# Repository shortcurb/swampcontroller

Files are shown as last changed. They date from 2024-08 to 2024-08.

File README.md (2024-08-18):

# swampcontroller
Hardware and software for controlling evaporative coolers with MQTT and relays

I live in a climate where using evaporative (swamp) coolers to cool dwellings is a generally effective possibility. I have two swamp coolers. I like them because they are cheap to run, cheap and easy to maintain, and if one breaks, I can almost certainly fix it myself, rather than calling a contractor.

My swamp coolers electrical components consist of a water pump and a 1/4HP blower fan with high and low speed settings. I designed this PCB to use an ESP8266 to control three off-board 12V automotive relays, which was easier than trying to figure out how to manage 10A on my little 1oz copper PCB traces.

If anyone is interested, I have 3 remaining unpopulated PCB boards I would be happy to sell/ship somewhere

Hardware features:
* ESP8266 header
* LM2596 (eBay/Amazon THT variant) 4V-40V input
* power header
* 3 relay-control headers

Hardware Problems:
* The pins that control speedheader and fanheader are currently wired to pins that control the flash on an ESP8266. Need to cut the trace and install a jumper wire somewhere else to control them correctly.

Software features:
* State, command, and response MQTT feeds
* State feed publishes the state of the swamper regularly
* Subscribes to command feed to listen for commands
* Response feed is for sending responses to commands
* 5s delay after receiving a command, to prevent changing motor/pump electricity too quickly
Software Problems:
* If the MQTT broker goes down, or Wifi goes down, the device will eventually crash and turn off the blower and fan. This is intended as a purely wifi-controllable device, so its user preference to decide whether failing off is better than failing on. This is kind of an odd edge case, in that my wifi/broker generally only go down if my house electricity goes down, and if my house doesn't have electricity, the swamper isn't running either.

Closing thoughts:
* I assembled the components and relays and a 12V wall wart adapter and cut up some old extension wire and wired everything up in a waterproof junction box and mounted it just below my swamp cooler, powered via an external outlet. Its been working great for the last month!

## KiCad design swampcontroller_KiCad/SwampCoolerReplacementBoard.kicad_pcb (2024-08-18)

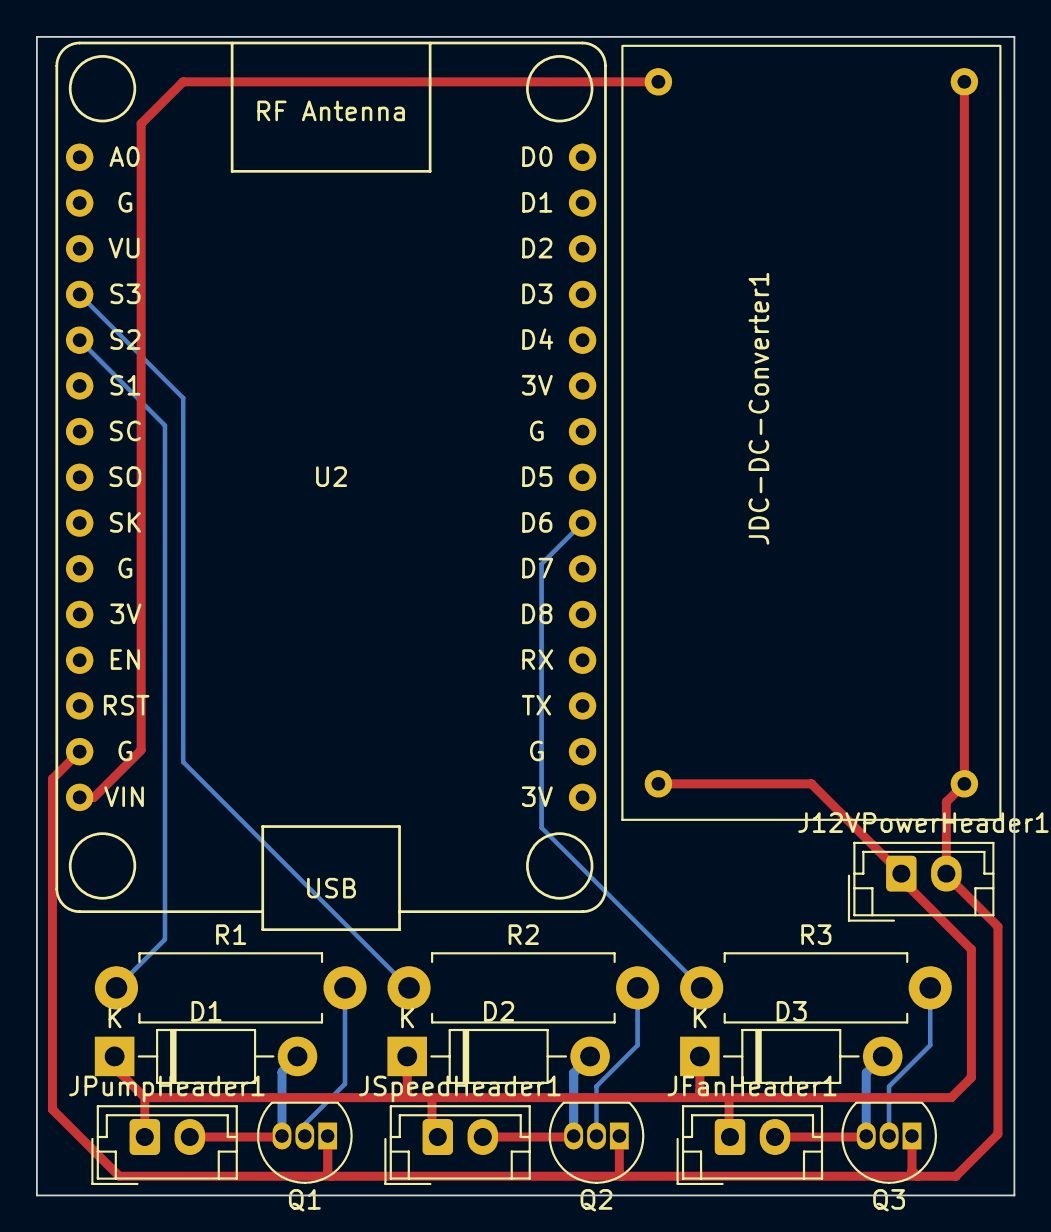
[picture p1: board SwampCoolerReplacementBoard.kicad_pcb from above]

Board: 2 copper layers, 54.3 x 64.4 mm, 15 parts (0 on the bottom side), 12 nets.

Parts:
D1, D2, D3: 1N4007; D_DO-41_SOD81_P10.16mm_Horizontal
J12VPowerHeader1: Conn_01x02; JST_EH_B2B-EH-A_1x02_P2.50mm_Vertical
JDC-DC-Converter1: Conn_01x04; XL6009E1 DC-DC
JFanHeader1: Conn_01x02; JST_EH_B2B-EH-A_1x02_P2.50mm_Vertical
JPumpHeader1: Conn_01x02; JST_EH_B2B-EH-A_1x02_P2.50mm_Vertical
JSpeedHeader1: Conn_01x02; JST_EH_B2B-EH-A_1x02_P2.50mm_Vertical
Q1, Q2, Q3: 2N7000; TO-92_Inline
R1, R2, R3: 470; R_Axial_DIN0411_L9.9mm_D3.6mm_P12.70mm_Horizontal
U2: NodeMCU1.0(ESP-12E); NodeMCU1.0(12-E)

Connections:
+5V: JDC-DC-Converter1.3, U2.15 (VIN)
+12V: D1.1 (K), D2.1 (K), D3.1 (K), J12VPowerHeader1.1, JDC-DC-Converter1.1, JFanHeader1.1, JPumpHeader1.1, JSpeedHeader1.1
FanRelay: D3.2 (A), JFanHeader1.2, Q3.3 (D)
FanSelect: R2.1, U2.4 (SD3(GPIO10))
FanTrigger: R3.1, U2.22 (D6(GPIO12))
GND: J12VPowerHeader1.2, JDC-DC-Converter1.2, JDC-DC-Converter1.4, Q1.1 (S), Q2.1 (S), Q3.1 (S), U2.14 (GND)
unnamed: Q1.2 (G), R1.2
unnamed: D1.2 (A), JPumpHeader1.2, Q1.3 (D)
unnamed: Q2.2 (G), R2.2
unnamed: Q3.2 (G), R3.2
PumpTrigger: R1.1, U2.5 (SD2(GPIO9))
SpeedRelay: D2.2 (A), JSpeedHeader1.2, Q2.3 (D)

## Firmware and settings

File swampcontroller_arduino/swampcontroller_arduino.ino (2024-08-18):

#include <ESP8266WiFi.h>
#include "Adafruit_MQTT.h"
#include "Adafruit_MQTT_Client.h"
#include "secrets.h"
// secrets.h includes wifi credentials, MQTT credentials, plus the subscribe topics and publish topics
#define HEARTBEAT_INTERVAL 6000 // 6 seconds

const int fantriggerpin = 14; 
const int fanselectpin = 12; 
const int pumptriggerpin = 13; 

const unsigned long heartbeatInterval = 5000;
unsigned long lastHeartbeat = 0;

WiFiClient client;
Adafruit_MQTT_Client mqtt(&client, mqttserv, mqttport, mqttuser, mqttpass);

/****************************** Feeds ***************************************/
Adafruit_MQTT_Subscribe swampcommandfeed = Adafruit_MQTT_Subscribe(&mqtt, mqttuser swampcommandfeedstr);
Adafruit_MQTT_Publish swampresponsefeed = Adafruit_MQTT_Publish(&mqtt, mqttuser swampresponsefeedstr);
Adafruit_MQTT_Publish swampstatefeed = Adafruit_MQTT_Publish(&mqtt, mqttuser swampstatefeed);

/*************************** Sketch Code ************************************/

unsigned long lastReconnectAttempt = 0;

void setup() {

  // Need to set pins low when first booting. Low is relay deactivated.
  // Otherwise, if the wifi was down, your swamp cooler would turn on and remain on forever!!
  Serial.println("Setting pins");
  pinMode(fantriggerpin, OUTPUT);
  pinMode(fanselectpin, OUTPUT);
  pinMode(pumptriggerpin, OUTPUT);
  digitalWrite(fantriggerpin,LOW);
  digitalWrite(fanselectpin,LOW);
  digitalWrite(pumptriggerpin,LOW);

  Serial.begin(115200);
  delay(10);
  Serial.println();
  
  connectToWiFi();
    
  Serial.println("Subscribing to feeds");
  mqtt.subscribe(&swampcommandfeed);

  Serial.println("Setup complete");
}

void loop() {
  // Ensure we're connected to WiFi and the MQTT server
  ensureConnected();

  // Read subscription
  Adafruit_MQTT_Subscribe *subscription;
  while ((subscription = mqtt.readSubscription(100))) {
    if (subscription == &swampcommandfeed) {
      Serial.print(F("Got: "));
      Serial.println((char *)swampcommandfeed.lastread);

      int pins[] = {-1,-1,-1};
      if      (strcmp((char*)swampcommandfeed.lastread, "SWAMP_HIGH") == 0){pins[0]=1; pins[1] = 1; pins[2] = 1;}
      else if (strcmp((char*)swampcommandfeed.lastread, "SWAMP_LOW")  == 0){pins[0]=1; pins[1] = 1; pins[2] = 0;}
      else if (strcmp((char*)swampcommandfeed.lastread, "FAN_HIGH")   == 0){pins[0]=0; pins[1] = 1; pins[2] = 1;}  
      else if (strcmp((char*)swampcommandfeed.lastread, "FAN_LOW")    == 0){pins[0]=0; pins[1] = 1; pins[2] = 0;}
      else if (strcmp((char*)swampcommandfeed.lastread, "PUMP_ON")    == 0){pins[0]=1; pins[1] = 0; pins[2] = -1;}
      else if (strcmp((char*)swampcommandfeed.lastread, "OFF")        == 0){pins[0]=0; pins[1] = 0; pins[2] = -1;}

      switchRelays(pins);
      char response[100];
      sprintf(response, "pump:%d, fan trigger:%d, fan select:%d", pins[0], pins[1], pins[2]);
      swampresponsefeed.publish(response);
      sendHeartbeat();
      mqtt.disconnect();
      delay(5000);
    }
  }

  // Send heartbeat at regular intervals
  unsigned long now = millis();
  if (now - lastHeartbeat > HEARTBEAT_INTERVAL) {
    lastHeartbeat = now;
    sendHeartbeat();
  }
}

void sendHeartbeat() {
  unsigned long currentMillis = millis();
  char heartbeatMsg[100];
  const char* pinState = readPins();
  snprintf(heartbeatMsg, sizeof(heartbeatMsg), "{\"Current State\": \"%s\", \"Heartbeat\": %lu}", pinState, currentMillis);
  Serial.println(heartbeatMsg);
  swampstatefeed.publish(heartbeatMsg);
}

const char* readPins() {
  static char currentstate[20]; // Static to persist the state outside this function
  int pin1 = digitalRead(pumptriggerpin);
  int pin2 = digitalRead(fantriggerpin);
  int pin3 = digitalRead(fanselectpin);
  
  String pinstates = String(pin1) + String(pin2) + String(pin3);
  
  if      (pinstates == "111") { strcpy(currentstate, "SWAMP_HIGH"); }
  else if (pinstates == "110") { strcpy(currentstate, "SWAMP_LOW"); }
  else if (pinstates == "011") { strcpy(currentstate, "FAN_HIGH"); }
  else if (pinstates == "010") { strcpy(currentstate, "FAN_LOW"); }
  else if (pinstates == "101" || pinstates == "100") { strcpy(currentstate, "PUMP_ON"); }
  else if (pinstates == "001" || pinstates == "000") { strcpy(currentstate, "OFF"); }
  else { strcpy(currentstate, "UNKNOWN"); }
  
  return currentstate;
}


void switchRelays(int pins[]){
  if (pins[0] == 1 || pins[0] == 0){digitalWrite(pumptriggerpin,pins[0]);}
  if (pins[1] == 1 || pins[1] == 0){digitalWrite(fantriggerpin,pins[1]);}
  if (pins[2] == 1 || pins[2] == 0){digitalWrite(fanselectpin,pins[2]);}
}


void MQTT_connect() {
  int8_t ret;

  if (mqtt.connected()) {
    return;
  }

  Serial.print("Connecting to MQTT... ");

  while ((ret = mqtt.connect()) != 0) { // connect will return 0 for connected
    Serial.println(mqtt.connectErrorString(ret));
    Serial.println("Retrying MQTT connection in 5 seconds...");
    mqtt.disconnect();
    delay(5000);  // wait 5 seconds
    yield();  // Reset the watchdog timer
  }
  Serial.println("MQTT connected");
}


void ensureConnected() {
  if (WiFi.status() != WL_CONNECTED) {
    connectToWiFi();
  }
  
  if (!mqtt.connected()) {
    unsigned long now = millis();
    if (now - lastReconnectAttempt > 5000) {
      lastReconnectAttempt = now;
      if (mqtt.connect()) {
        lastReconnectAttempt = 0;
      }
    }
  }
}


void connectToWiFi() {
  // Check if the ESP is already connected to WiFi
  if (WiFi.status() == WL_CONNECTED) {
    return; // Already connected, so exit the function
  }
  Serial.print("Connecting to WiFi...");
  WiFi.begin(ssid, wifipass);

  // Wait for connection
  while (WiFi.status() != WL_CONNECTED) {
    delay(500);
    Serial.print(".");
  }
  Serial.println("WiFi connected");
  Serial.print("IP address: ");
  Serial.println(WiFi.localIP());
}

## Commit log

2024-08-18 first hw + sw push
    [SwampCoolerReplacementBoard.kicad_pcb, SwampCoolerReplacementBoard.kicad_sch]
2025-03-28 updated with pcb schematics zip
